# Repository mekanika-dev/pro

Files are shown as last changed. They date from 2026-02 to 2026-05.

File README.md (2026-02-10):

# Pro CNC (Mk2)

> A robust CNC machine for precise milling featuring ballscrews and prismatic linear rails for superior accuracy across different jobs and materials.

- [Assembly Guide & Documentation](https://support.mekanika.io/products/pro-cnc-mk2)
- [Shop](https://www.mekanika.io/en/store/be/pro/)
- [Contact](https://www.mekanika.io/contact-us/)

Mekanika Pro CNC (Mk2)

## Repository Structure

- **`bom/`** - Bill of Materials
- **`cad/`** - CAD files
- **`docs/`** - Documentation files

The Bill of Materials is available as a CSV file, which is dynamically updated from our ERP. We recommend using this **[web viewer](https://mekanika-dev.github.io/data-sync-actions/odoo/bom-viewer.html)** to browse its content.

All 3D assembly files are made in STEP format and compatible with many CAD software. Please note that you will need Git LFS installed to clone or pull the repo correctly, since these files exceed 100MB.

The design files can also be viewed in web browsers using these links:

- [Pro-S](https://a360.co/44uoy98)
- [Pro-M](https://a360.co/3PJz4Fp)
- [Pro-L](https://a360.co/46BXE0F)
- [Pro Control Unit](https://a360.co/4mlOA7u)

## Assembly Guide

The assembly guide is available on our [support website](https://support.mekanika.io/products/pro-cnc-mk2). If you have feedback or want to raise an issue about a specific assembly step, you can use the feedback buttons available on each step's page.

## Community

Mekanika encourages collaborative design and innovation. We welcome:

- Designers and engineers to contribute
- Feedback on design variations
- Any discussions around or products and potential improvements

Don't hesitate to join us on our [Discord](https://discord.gg/n7RsBtUdGc)

## License

This project is licensed under the **CERN Open Hardware Licence Version 2 - Strongly Reciprocal** ([CERN-OHL-S v2](https://ohwr.org/cern_ohl_s_v2.pdf))

For the complete license terms, see REUSE.toml

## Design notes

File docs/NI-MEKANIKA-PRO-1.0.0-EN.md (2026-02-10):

---
title: "USER MANUAL: CNC PRO"
css: style.css
---

<div class="cover-page" style="text-align: center;">

Logo Mekanika

<h4 style="margin-bottom: 0;">3-AXIS CNC MILLING MACHINE</h4>

<hr style="width: 200px; margin: 10px auto; color:#000 !important;"/>

<h4 style="margin-top: 0;">PRO MODEL V1.0</h4>

Pro ISO View

**ORIGINAL MANUAL**
<br/>
Version: 1.0.0-EN
<br/>
Revision Date: November 2025

</div>

## TABLE OF CONTENTS

#### 1. GENERAL INFORMATION

<ul style="list-style-type: none;">
  <li>1.1 <a href="#11-manufacturer-identification">Manufacturer identification</a></li>
  <li>1.2 <a href="#12-ce-declaration-of-conformity">CE Declaration of Conformity</a></li>
  <li>1.3 <a href="#13-intended-use">Intended use</a>
    <ul style="list-style-type: none;">
      <li>1.3.1 <a href="#131-normal-use">Normal use</a></li>
      <li>1.3.2 <a href="#132-prohibited-uses">Prohibited uses</a></li>
    </ul>
  </li>
  <li>1.4 <a href="#14-authorized-personnel">Authorized personnel</a>
    <ul style="list-style-type: none;">
      <li>1.4.1 <a href="#141-minimum-requirements">Minimum requirements</a></li>
      <li>1.4.2 <a href="#142-restrictions">Restrictions</a></li>
    </ul>
  </li>
</ul>

#### 2. SAFETY

<ul style="list-style-type: none;">
  <li>2.1 <a href="#21-safety-instructions-by-risk-level">Safety instructions by risk level</a></li>
  <li>2.2 <a href="#22-personal-protective-equipment">Personal protective equipment</a>
    <ul style="list-style-type: none;">
      <li>2.2.1 <a href="#221-mandatory-ppe">Mandatory PPE</a></li>
      <li>2.2.2 <a href="#222-dress-code">Dress code</a></li>
    </ul>
  </li>
  <li>2.3 <a href="#23-safety-devices">Safety devices</a>
    <ul style="list-style-type: none;">
      <li>2.3.1 <a href="#231-emergency-stop">Emergency stop</a></li>
      <li>2.3.2 <a href="#232-limit-switches">Limit switches</a></li>
      <li>2.3.3 <a href="#233-dust-shoe">Dust shoe</a></li>
    </ul>
  </li>
</ul>

#### 3. TECHNICAL DESCRIPTION

<ul style="list-style-type: none;">
  <li>3.1 <a href="#31-overview">Overview</a>
    <ul style="list-style-type: none;">
      <li>3.1.1 <a href="#311-axis-diagram">Axis diagram</a></li>
      <li>3.1.2 <a href="#312-control-box-diagram">Control box diagram</a></li>
    </ul>
  </li>
  <li>3.2 <a href="#32-technical-specifications">Technical specifications</a></li>
</ul>

#### 4. INSTALLATION & ASSEMBLY

<ul style="list-style-type: none;">
  <li>4.1 <a href="#41-unpacking-and-inspection">Unpacking and inspection</a>
    <ul style="list-style-type: none;">
      <li>4.1.1 <a href="#411-upon-receipt">Upon receipt</a></li>
      <li>4.1.2 <a href="#412-kit-inventory">Kit inventory</a></li>
    </ul>
  </li>
  <li>4.2 <a href="#42-assembly">Assembly</a>
    <ul style="list-style-type: none;">
      <li>4.2.1 <a href="#421-preparation">Preparation</a></li>
    </ul>
  </li>
  <li>4.3 <a href="#43-installation">Installation</a>
    <ul style="list-style-type: none;">
      <li>4.3.1 <a href="#431-recommended-layout">Recommended layout</a></li>
      <li>4.3.2 <a href="#432-room-requirements">Room requirements</a></li>
    </ul>
  </li>
</ul>

#### 5. INITIAL STARTUP

<ul style="list-style-type: none;">
  <li>5.1 <a href="#51-preliminary-checks">Preliminary checks</a>
    <ul style="list-style-type: none;">
      <li>5.1.1 <a href="#511-safety-checklist">Safety checklist</a></li>
    </ul>
  </li>
  <li>5.2 <a href="#52-first-power-on">First power on</a>
    <ul style="list-style-type: none;">
      <li>5.2.1 <a href="#521-startup-sequence">Startup sequence</a></li>
    </ul>
  </li>
  <li>5.3 <a href="#53-functional-test">Functional test</a></li>
</ul>

#### 6. OPERATION

<ul style="list-style-type: none;">
  <li>6.1 <a href="#61-checklist-for-safe-machine-operation">Checklist for safe machine operation</a>
    <ul style="list-style-type: none;">
      <li>6.1.1 <a href="#611-daily-startup">Daily startup</a></li>
    </ul>
  </li>
  <li>6.2 <a href="#62-workpiece-clamping">Workpiece clamping</a>
    <ul style="list-style-type: none;">
      <li>6.2.1 <a href="#621-fixation-systems-supplied-with-base-kit">Fixation systems supplied with base kit</a></li>
      <li>6.2.2 <a href="#622-fixation-rules">Fixation rules</a></li>
    </ul>
  </li>
  <li>6.3 <a href="#63-tool-installation">Tool installation</a>
    <ul style="list-style-type: none;">
      <li>6.3.1 <a href="#631-tool-change">Tool change</a></li>
      <li>6.3.2 <a href="#632-tool-length-measurement">Tool length measurement</a></li>
    </ul>
  </li>
  <li>6.4 <a href="#64-programming-and-machining">Programming and machining</a>
    <ul style="list-style-type: none;">
      <li>6.4.1 <a href="#641-accepted-formats">Accepted formats</a></li>
      <li>6.4.2 <a href="#642-operating-modes">Operating modes</a></li>
    </ul>
  </li>
  <li>6.5 <a href="#65-monitoring-during-machining">Monitoring during machining</a>
    <ul style="list-style-type: none;">
      <li>6.5.1 <a href="#651-control-points">Control points</a></li>
      <li>6.5.2 <a href="#652-anomalies-and-actions">Anomalies and actions</a></li>
    </ul>
  </li>
</ul>

#### 7. ADD-ONS AND OPTIONS

<ul style="list-style-type: none;">
  <li>7.1 <a href="#71-vacuum-table">Vacuum table</a>
    <ul style="list-style-type: none;">
      <li>7.1.1 <a href="#711-specifications">Specifications</a></li>
      <li>7.1.2 <a href="#712-operation">Operation</a></li>
    </ul>
  </li>
  <li>7.2 <a href="#72-dust-collection-kit">Dust collection kit</a>
    <ul style="list-style-type: none;">
      <li>7.2.1 <a href="#721-specifications">Specifications</a></li>
    </ul>
  </li>
  <li>7.3 <a href="#73-laser-module-lsr">Laser module (LSR)</a>
    <ul style="list-style-type: none;">
      <li>7.3.1 <a href="#731-specifications">Specifications</a></li>
    </ul>
  </li>
</ul>

#### 8. MAINTENANCE & TROUBLESHOOTING

<ul style="list-style-type: none;">
  <li>8.1 <a href="#81-preventive-maintenance-plan">Preventive maintenance plan</a></li>
  <li>8.2 <a href="#82-lubrication">Lubrication</a></li>
  <li>8.3 <a href="#83-spare-parts">Spare parts</a></li>
</ul>

#### 9. TROUBLESHOOTING

<ul style="list-style-type: none;">
  <li>9.1 <a href="#91-troubleshooting-and-diagnostics">Troubleshooting and diagnostics</a></li>
  <li>9.2 <a href="#92-technical-support">Technical support</a>
    <ul style="list-style-type: none;">
      <li>9.2.1 <a href="#921-before-contacting-support">Before contacting support</a></li>
    </ul>
  </li>
</ul>

#### 10. TRANSPORTATION & STORAGE

<ul style="list-style-type: none;">
  <li>10.1 <a href="#101-machine-transportation">Machine Transportation</a></li>
  <li>10.2 <a href="#102-packaging--waste">Packaging & Waste</a></li>
  <li>10.3 <a href="#103-storage">Storage</a></li>
</ul>

## 1. GENERAL INFORMATION {#1-general-information}

### 1.1 Manufacturer identification {#11-manufacturer-identification}

**Mekanika SRL**

Chaussée de Mons 1281  
1070 Anderlecht, Belgium  
VAT No: BE0740501760

**Contact:**

<ul style="list-style-type: none;">
<li><i class="fas fa-envelope" style="color: #2196f3;"></i> info@mekanika.io</li>
<li><i class="fas fa-globe" style="color: #2196f3;"></i> www.mekanika.io</a></li>
</ul>

### 1.2 CE Declaration of Conformity {#12-ce-declaration-of-conformity}

This machine complies with the following European directives:

- **2006/42/EC** - Machinery Directive
- **2014/30/EU** - Electromagnetic Compatibility (EMC) Directive

**Applied harmonized standards:**

- **EN ISO 12100:2010** - Safety of machinery, General principles
- **EN 60204-1:2006** - Electrical safety of machinery
- **EN ISO 13850:2015** - Emergency stop function
- **EN 848-3:2012** - Safety of woodworking machines (partially)
- **EN 61000-6-1** - EMC Immunity
- **EN 61000-6-3** - EMC Emissions

The original declaration of conformity is provided with this machine.

### 1.3 Intended use {#13-intended-use}

Please read this operating manual and all accompanying documents in their entirety before commissioning the machine.

If in doubt or if you need additional information, do not hesitate to contact us before using the machine.

#### 1.3.1 Normal use {#131-normal-use}

The MEKANIKA PRO CNC milling machine is a 3-axis CNC machine designed for:

<ul style="list-style-type: none; margin-left: 0.75em">
  <li><i class="fas fa-square-check" style="color: #4EBD7D;"></i> Machining wood and derivatives (plywood, MDF, OSB)</li>
  <li><i class="fas fa-square-check" style="color: #4EBD7D;"></i> Machining plastics (PVC, acrylic, polycarbonate)</li>
  <li><i class="fas fa-square-check" style="color: #4EBD7D;"></i> Machining non-ferrous metals (aluminum, brass)</li>
  <li><i class="fas fa-square-check" style="color: #4EBD7D;"></i> Machining composite materials (with special precautions)</li>
</ul>

#### 1.3.2 Prohibited uses {#132-prohibited-uses}

The following uses are **PROHIBITED**:

<ul style="list-style-type: none; margin-left: 0.75em">
  <li><i class="fas fa-xmark" style="color: #d32f2f;"></i> Machining unknown composite materials or those containing asbestos</li>
  <li><i class="fas fa-xmark" style="color: #d32f2f;"></i> Use in explosive atmospheres</li>
  <li><i class="fas fa-xmark" style="color: #d32f2f;"></i> Outdoor use or in humid environments</li>
  <li><i class="fas fa-xmark" style="color: #d32f2f;"></i> Machining improperly secured workpieces</li>
  <li><i class="fas fa-xmark" style="color: #d32f2f;"></i> Machining beyond the machine's technical capabilities</li>
</ul>

### 1.4 Authorized personnel {#14-authorized-personnel}

#### 1.4.1 Minimum requirements {#141-minimum-requirements}

- **Minimum age:** 16 years
- **Required training:**
  - Complete reading of this manual
  - Completed online training (series of free video tutorials)
  - Basic CAM knowledge
- **Physical abilities:**
  - Normal or corrected vision
  - Normal or aided hearing
  - Sufficient mobility to access the emergency stop

#### 1.4.2 Restrictions {#142-restrictions}

- Prohibited for untrained persons
- Prohibited for persons under influence (alcohol, drugs, medication)
- Mandatory supervision for persons learning to operate the machine

## 2. SAFETY {#2-safety}

Read the entire operating manual to familiarize yourself with the machine's features and how to use them. Improper operation of the machine can result in damage to the machine, your personal property, and cause serious injury, electric shock and/or fire.

**It is imperative to comply at all times with the safety instructions listed in this operating manual.**

### 2.1 Safety instructions by risk level {#21-safety-instructions-by-risk-level}

The following terms are used in this operating manual to indicate different levels of potential danger when using this machine. Safety symbols and their explanations require your attention.

Safety warnings do not eliminate any danger. The instructions or warnings they provide do not replace appropriate preventive measures.

> **<i class="fas fa-ban" style="color: #d32f2f;"></i> DANGER** - _Instructions which, if not properly followed, create a probability of property damage, collateral damage, serious injury or death, or create a high probability of superficial injury._

| **RISK TYPE** | **SAFETY INSTRUCTIONS** |
| :--- | :--- |
| **Risk of electrocution** | Machine plugs must match the power outlet used. Never modify the plug in any way. Do not use adapter plugs with grounded machines. |
| **Risk of electrocution - indirect contact** | An insulation fault can energize normally non-conductive metal parts (chassis, structure, housing). Causes include: cable wear in cable carriers, moisture infiltration, accumulation of conductive dust, failed components, or mechanical damage. Never use the machine if: <br/> - The differential circuit breaker trips repeatedly; <br/> - Electric arc traces are visible (blackening, burning smell); <br/> - Moisture/condensation is visible in the housing. |
| **Toxic dust** | Some dust created when machining certain types of materials may contain chemicals known to cause cancer, birth defects or other reproductive harm. Always research the material you have on hand before machining it. Here are some examples of these chemicals: lead from non-ferrous metals containing lead, carbonate from carbon fiber, arsenic and chromium from chemically treated wood.<br><br>The risk you run from exposure varies depending on how often you perform this type of work. To reduce your exposure to these chemicals: work in a well-ventilated area and use approved safety equipment, such as dust masks specifically designed to filter microscopic particles. |
| **Explosive atmosphere** | Do not operate the machine in explosive atmospheres, such as in the presence of flammable liquids, gases or dust. Machines can create sparks that can ignite dust or fumes. |

> **<i class="fas fa-exclamation-triangle" style="color: #ff9800;"></i> WARNING** - _Instructions which, if not properly followed, create a probability of property damage and a possibility of serious injury._

| **RISK TYPE** | **SAFETY INSTRUCTIONS** |
| :--- | :--- |
| **Dress code** | Dress appropriately. Do not wear loose clothing or jewelry. Pin your hair above your shoulders so it cannot get caught in linear guides or moving parts. |
| **Vigilance** | Stay alert, watch what you are doing and use common sense when operating a machine. Do not use a machine when you are tired and/or under the influence of drugs, alcohol or medication. A moment of inattention when using a machine can result in serious injury. |
| **Personal protection**  | Use personal protective equipment. Always wear eye protection. Protective equipment, such as a dust mask or appropriate hearing protection, reduces the risk of injury. |
| **Machine control** | This machine is computer controlled. During operation, it cannot be directly controlled. Lack of caution or expertise and program errors can lead to unexpected movements. |
| **Rotating tool** | Do not touch the rotating tool area. The proximity of the rotating tool to your hand is not always easy to detect. |
| **Tool jam** | If the workpiece or end mill jams, immediately press the emergency stop button. Wait until all moving parts have stopped and the spindle is off, then release the stuck material. Do not attempt to do this while the spindle is running. |
| **Hot tools** | Do not touch the end mill or collet after use. After use, they are too hot to touch with bare hands. |
| **Hot surfaces** | Do not touch the motors, as they can heat up during machine operation. |
| **Tool handling** | Be careful when handling tools, they can be very sharp. Never place any part of the tool or accessories in your mouth, as this can result in serious injury. |
| **Workpiece fixation** | Before starting any machining operation, always secure your workpiece properly. Never try to hold the workpiece by hand or with accessories. These tools can easily jam in the material and can kick back, resulting in loss of control and serious injury. |
| **Limit sensors** | Never try to reach the limit sensors when the machine is moving, this could result in crushing your hand or fingers. |
| **Prohibited modifications** | Do not modify your machine, or use it in a manner not intended by the manufacturer. Any alteration or modification constitutes misuse and can result in serious injury. |
| **Lockout** | Disconnect the plug from the power source before making adjustments, changing accessories or disassembling the machine. |
| **Machine access** | Keep the machine out of reach of children and do not allow persons unfamiliar with these instructions to use the machine. Machines are dangerous in the hands of untrained users. |
| **Safety distance** | Keep children and bystanders at a distance. Distractions can cause you to lose control and cause accidents. |

> **<i class="fas fa-info-circle" style="color: #2196f3;"></i> CAUTION** - _Instructions which, if not properly followed, create a possibility of property damage and a possibility of minor injury._

| **RISK TYPE** | **SAFETY INSTRUCTIONS** |
| :--- | :--- |
| **Mandatory training** | All persons using the machine must have read and fully understood all relevant safety and operating instructions. Any misunderstanding can result in injury. |
| **Cleanliness and lighting** | Keep the work area clean and well lit. Cluttered or dark areas are prone to accidents. |
| **Indoor use** | Only operate the machine in indoor spaces. |
| **Moisture protection** | Do not expose the machine to moisture. The machine can only be used indoors. |
| **Supervision** | Do not leave the machine running unattended, and cut the spindle power if you leave. The machine is only secure when it is completely stopped and unplugged from the mains. |
| **Proper use** | Use the machine and its accessories in accordance with this manual, taking into account the working conditions and the work to be performed. Using the machine for operations other than those intended can result in a dangerous situation with a high probability of injury. |
| **Tool condition** | Never use dull or damaged end mills. Damaged end mills can break during use. Dull end mills require more force to cut, which can result in end mill breakage. |
| **Machining parameters** | The speed and feed rate of the end mill during engraving, profiling or cutting are very important. Always follow the recommended speed and feed rate for a particular end mill/machine/operation configuration. |
| **Ventilation** | Remember to clean the ventilation openings of the control boxes using compressed air. Excessive dust accumulation inside the boxes can cause electrical failures. |
| **Preventive maintenance** | Properly maintain the tools you use. Check for misalignment or binding of moving parts, broken parts and any other condition that may affect the machine's operation. If damaged, have the machine repaired before using it. Many accidents are caused by poorly maintained machines. |
| **Repairs** | Have your machine repaired by a qualified repairer using only identical spare parts. |

### 2.2 Personal protective equipment {#22-personal-protective-equipment}

#### 2.2.1 Mandatory PPE {#221-mandatory-ppe}

| Equipment | Use | Pictogram |
| :--- | :--- | :---: |
| **Safety glasses** | Recommended during machining |  Safety glasses  |
| **Hearing protection** | Recommended during machining, mandatory if noise level > 80 dB(A) | Hearing protection |
| **Gloves** | Recommended when handling parts/tools | Gloves |
| **FFP2 mask** | Mandatory when machining composite materials | FFP2 mask |
| **Safety shoes** | Recommended for all work in front of a machine | Safety shoes |

#### 2.2.2 Dress Code {#222-dress-code}

**<i class="fas fa-square-check" style="color: #4EBD7D;"></i> MANDATORY:**

- Fitted clothing
- Short sleeves or rolled up
- Long hair tied back or under cap

**<i class="fas fa-xmark" style="color: #d32f2f;"></i> PROHIBITED:**

- Jewelry (rings, necklaces, bracelets)
- Loose clothing
- Ties, scarves
- Gloves during machining

### 2.3 Safety devices {#23-safety-devices}

#### 2.3.1 Emergency stop {#231-emergency-stop}

**Characteristics:**

- Type: Lockable mushroom button
- Color: Red on yellow background
- Standard: EN ISO 13850:2015
- Position: Front face, easily accessible

**Operation:**

1. **Activation:** Press the red button
   - Immediate stop of all movements
   - Spindle shutdown
   - Machine control software lockout
2. **Reset:** Turn the button clockwise
   - The program must be restarted manually

#### 2.3.2 Limit switches {#232-limit-switches}

**Configuration:**

- 6 NC PNP inductive sensors
- 2 sensors on X and Y axes (min/max) with AND logic for redundant safety

**Triple function:**

1. **Homing:** Machine referencing at startup
2. **Safety:** Emergency stop if limit reached
3. **Square gantry:** Gantry squaring

#### 2.3.3 Dust shoe {#233-dust-shoe}

**Dual function:**

- Protection against tool access
- Chip and dust collection

> **<i class="fas fa-info-circle" style="color: #2196f3;"></i> CAUTION** - _Never remove the shoe during machining_

## 3. TECHNICAL DESCRIPTION {#3-technical-description}

### 3.1 Overview {#31-overview}

The MEKANIKA PRO is a 3-axis CNC milling machine, allowing material to be machined by moving along the X, Y and Z axes, or a combination of these by linear interpolation.

#### 3.1.1 Axis diagram {#311-axis-diagram}

Axes diagram

**Axes terminology:**

- **X axis:** Lateral movement (left-right)
- **Y axis:** Longitudinal movement (front-back)
- **Z axis:** Vertical movement (up-down)

#### 3.1.2 Control box diagram {#312-control-box-diagram}

Control box diagram

**Connector description:**

- **1**: Fan
- **2**: Motors
- **3**: Limit switches
- **4**: Emergency stop
- **5**: Tool probe (Input 1)
- **6**: Spindle control
- **7**: Input 2
- **8**: Input 3
- **9**: Laser control
- **10**: HDMI
- **11**: USB 2.0
- **12**: Ethernet
- **13**: Power supply
- **14**: Ground

### 3.2 Technical specifications {#32-technical-specifications}

| **CHARACTERISTIC** | **VALUE** |
| :--- | :--- |
| **MACHINE DIMENSIONS** | |
| Overall dimensions | - S: 960 x 960 x 650 mm <br/> - M: 1360 x 960 x 650 mm <br/> - L: 1250 x 1250 x 650 mm |
| Total weight | - S: 55 kg <br/> - M: 62 kg <br/> - L: 69 kg |
| **WORKING AREA** | |
| Machinable surface | - S: 630 x 630 mm <br/> - M: 630 x 1030 mm <br/> - L: 1030 x 1030 mm |
| Table-spindle distance (max) | 105 mm |
| **PERFORMANCE** | |
| Max travel speed | 10000 mm/min |
| Recommended machining speed | 100 - 7000 mm/min |
| **MECHANICS** | |
| Linear guides | Double prismatic rail HGR20 |
| X, Y & Z transmission | 16 mm ball screws (C7) |
| Structure | Aluminum profiles + steel plates |
| **MOTORS** | |
| X, Y & Z motors | NEMA23 5A |
| **SPINDLE** | |
| Power | 2.2 kW |
| Cooling | Air |
| Rotation speed | 6000 - 24000 rpm |
| Collet | ER20 (1-13 mm) |
| Control | Variable frequency drive (VFD) |
| **ELECTRICAL** | |
| Power supply | 230V AC single phase, 50 Hz |
| Maximum power | 2.9 kW |
| Protection | 16A fuse, grounding mandatory |
| **ENVIRONMENT** | |
| Operating temperature | 5°C to 35°C |
| Relative humidity | 40-60% |
| Use | Indoor only |

## 4. INSTALLATION & ASSEMBLY {#4-installation--assembly}

### 4.1 Unpacking and inspection {#41-unpacking-and-inspection}

#### 4.1.1 Upon receipt {#411-upon-receipt}

**Check immediately:**

1. Condition of packaging (photos if damaged)
2. Presence of all packages (see delivery note)
3. Absence of apparent damage

#### 4.1.2 Kit inventory {#412-kit-inventory}

We strongly recommend that you inventory your kit before starting assembly. The list of parts grouped by package is available on our website:
<br>
<i class="fas fa-globe" style="color: #2196f3;"></i> [support.mekanika.io/products/pro-cnc-mk2/kit-content](https://support.mekanika.io/products/pro-cnc-mk2/kit-content)

### 4.2 Assembly {#42-assembly}

Please carefully follow our online assembly guide to properly assemble your Mekanika machine.
<br>
<i class="fas fa-globe" style="color: #2196f3;"></i> [support.mekanika.io/products/pro-cnc-mk2/assembly-guide](https://support.mekanika.io/products/pro-cnc-mk2/assembly-guide)

#### 4.2.1 Preparation {#421-preparation}

- **Required space:**
  - S: 1.96 × 1.96 m minimum
  - M: 2.36 x 1.96 m minimum
  - L: 2.36 x 2.36 m minimum
- **Estimated time:** 12 hours (alone) - 7 hours (2 people)
- **Required tools:** Supplied in the kit

> **<i class="fas fa-exclamation-triangle" style="color: #ff9800;"></i> RISK** - There is a non-negligible risk of heavy items falling during assembly. Please handle heavy parts with at least 2 people.

> **<i class="fas fa-info-circle" style="color: #2196f3;"></i> CAUTION** - Please follow the precise order of assembly steps to avoid risks of machine malfunction.

### 4.3 Installation {#43-installation}

#### 4.3.1 Recommended layout {#431-recommended-layout}

If you have the "table support" accessory, place the machine on a regular and stable floor.
If you do not have a "table support", place the machine on a robust and stable table allowing you to work at a good height. To ensure a comfortable working height, we recommend a working height of approximately 85 cm.

All moving parts of the machine must be able to operate without collision.

The machine must be easily accessible and usable. In particular, the emergency stop button must be easily accessible at all times.

**Zone description:**

- **1**: Operating zone
- **2**: Loading zone
- **3**: Maintenance and safety zone

Working area

#### 4.3.2 Room requirements {#432-room-requirements}

**Floor:**

- Flatness: < 5 mm/m
- Capacity: > 200 kg/m²
- Type: Concrete (recommended)

**Environment:**

- Temperature: 18-25°C ideal
- Humidity: 40-60%
- Lighting: > 500 lux on work area
- Ventilation: Adequate air renewal

## 5. INITIAL STARTUP {#5-initial-startup}

Before commissioning, the machine and all connected components must be properly wired and in perfect condition.

The operator must have read and understood the complete documentation for the relevant machine model and the corresponding instructions. In addition, they must have been trained in the operation of the machine and its accessories and must be familiar with the use of the CNC milling machine and PlanetCNC software in general.

### 5.1 Preliminary checks {#51-preliminary-checks}

> **<i class="fas fa-info-circle" style="color: #2196f3;"></i> CAUTION** - Never power on before these checks

#### 5.1.1 Safety checklist {#511-safety-checklist}

**Mechanical:**

<ul style="list-style-type: none; margin-left: 0.75em">
  <li><i class="fas fa-square-check" style="color: #4EBD7D;"></i> All fasteners tightened</li>
  <li><i class="fas fa-square-check" style="color: #4EBD7D;"></i> Freedom of axis movement (manual rotation)</li>
  <li><i class="fas fa-square-check" style="color: #4EBD7D;"></i> No abnormal play</li>
  <li><i class="fas fa-square-check" style="color: #4EBD7D;"></i> Guides and ball screws lubricated</li>
</ul>

**Electrical:**

<ul style="list-style-type: none; margin-left: 0.75em">
  <li><i class="fas fa-square-check" style="color: #4EBD7D; "></i> Ground continuity (< 0.1 Ω)</li>
  <li><i class="fas fa-square-check" style="color: #4EBD7D;"></i> Cable insulation</li>
  <li><i class="fas fa-square-check" style="color: #4EBD7D;"></i> Connections tight</li>
  <li><i class="fas fa-square-check" style="color: #4EBD7D;"></i> Mains differential protection tested</li>
</ul>

**Safety:**

<ul style="list-style-type: none; margin-left: 0.75em">
  <li><i class="fas fa-square-check" style="color: #4EBD7D;"></i> Emergency stop accessible and functional</li>
  <li><i class="fas fa-square-check" style="color: #4EBD7D;"></i> Limit switches connected</li>
  <li><i class="fas fa-square-check" style="color: #4EBD7D;"></i> Dust shoe installed</li>
  <li><i class="fas fa-square-check" style="color: #4EBD7D;"></i> Work area clear</li>
</ul>

### 5.2 First power on {#52-first-power-on}

#### 5.2.1 Startup sequence {#521-startup-sequence}

**1. Preparation**

- Area clear in front of and around the machine
- PPE worn
- Documentation within reach

**2. Power on**

- Check that emergency stop is unlocked
- Turn on control box
- Wait for Raspberry Pi initialization
- Wait for PlanetCNC to launch

**3. Initial checks**

- Control box fans rotating
- Limit switch indicators lit
- Touch screen on and PlanetCNC interface active
- Emergency stop button functional

### 5.3 Functional test {#53-functional-test}

We strongly recommend following our illustrated machine startup guide, available on our website:
<br>
<i class="fas fa-globe" style="color: #2196f3;"></i> [https://support.mekanika.io/products/pro-cnc-mk2/get-started](https://support.mekanika.io/products/pro-cnc-mk2/get-started)

This includes all the necessary information to test the machine on first use, as well as useful information about its operation and safety functions.

## 6. OPERATION {#6-operation}

The Pro CNC milling machine is intended for regular and professional use. Thanks to the machine's rigidity, it is possible to process a variety of different materials, such as wood and non-ferrous metals.

The plausible and reasonable scope of uses includes:

- Manual movement mode, using a digital "jog" to move the machine along its 3 axes independently.
- The automatic positioning procedure, performed by the user by clicking a digital button. This procedure moves the machine sequentially on each of its axes in the following order: Z, X, Y, until it encounters the limit switches.
- The tool length measurement procedure, activated by the user by clicking a digital button. This procedure lowers the machine at reduced speed along its Z axis until its tool contacts a removable sensor previously placed by the user.
- Normal operating mode, where the machine moves automatically according to a machine language, called G-code, previously loaded by the user.
- Manual control mode using a terminal allowing the machine to move according to a machine language, called G-code, entered directly by the user.

The plausible and reasonable scope of interventions includes:

- Manual movement of the machine to access certain areas.
- Changing the tool on the spindle.
- Attaching or removing the dust shoe.
- Attaching or removing the material to be machined.
- Launching, pausing and stopping the G-Code.
- Connecting/disconnecting external machine cables.
- Opening cable chains to access the machine.

### 6.1 Checklist for safe machine operation {#61-checklist-for-safe-machine-operation}

#### 6.1.1 Daily startup {#611-daily-startup}

**1. Inspection and equipment**

- Inspect equipment to ensure there are no obvious defects, damaged chucks, dull or cracked tools
- Use appropriate PPE (glasses, helmet, ...)
- Tie back long hair and wear well-fitted clothing and roll up your sleeves to avoid snags

**2. Machine preparation**

- Check where the emergency stop button is located
- Never connect or disconnect cables from the electronic box when the device is powered on
- Make sure the workpiece is firmly and securely clamped
- Check that the end mill is sharp and firmly tightened in the spindle chuck
- When handling or changing end mills, avoid touching the cutting edges
- Keep your hands free during manual adjustments

**3. During use**

- Never touch the machine when it is running and keep your hands away from any moving parts during machining
- Stay away from the machine when it is operational

**4. After machining**

- Use a brush or vacuum to clean chips from surfaces
- If linear guides and ball screws are dusty, blow them with compressed air to keep them clean and unobstructed by chips
- Clean the floor and work area around the machine
- Clean and store personal protective equipment
- Mark any defective equipment and contact us if you encounter a problem

**5. Normal shutdown**

1. Complete machining in progress
2. Stop the spindle
3. **Shut down Raspberry Pi** (proper shutdown)
4. Wait 30 seconds
5. Turn off control box

> **<i class="fas fa-info-circle" style="color: #2196f3;"></i> CAUTION** - Follow the order to avoid Raspberry Pi SD card corruption

**6. Emergency stop**

**In case of danger:**

1. **Immediately press** the red button
2. Cut power if necessary
3. Analyze the situation
4. Correct the problem
5. Reset (turn the button)
6. Redo a homing procedure

### 6.2 Workpiece clamping {#62-workpiece-clamping}

#### 6.2.1 Fixation systems supplied with base kit {#621-fixation-systems-supplied-with-base-kit}

**Wood screws:**

- For soft materials
- Direct screwing into spoilerboard
- Regular spacing

**Clamps with inserts:**

- For all materials
- M6 inserts in spoilerboard

#### 6.2.2 Fixation rules {#622-fixation-rules}

**<i class="fas fa-square-check" style="color: #4EBD7D;"></i> GOOD PRACTICES:**

- Minimum 4 fixation points
- Symmetrical distribution
- Verification before machining

**<i class="fas fa-xmark" style="color: #d32f2f;"></i> PROHIBITIONS:**

- Manual fixation
- Adhesive alone
- Cantilevered workpiece
- Excessive clamping (deformation)

> **<i class="fas fa-ban" style="color: #d32f2f;"></i> DANGER** - During machining, NEVER hold the workpiece by hand

### 6.3 Tool installation {#63-tool-installation}

#### 6.3.1 Tool change {#631-tool-change}

**Procedure:**

1. Wait for complete stop or machine pause
2. Move Z axis to high position
3. Unlock ER20 nut (keys provided)
4. Remove tool (gloves strongly recommended)
5. Insert new tool
6. Tighten firmly (without excess)

#### 6.3.2 Tool length measurement {#632-tool-length-measurement}

**With the supplied tool probe:**

1. Place the probe on the workpiece or spoilerboard (depending on the Z0 coordinate defined in the program)
2. Position the spindle above the probe
3. Press the tool length measurement icon
4. Slow automatic descent
5. Contact and memorization of the new Z0 position

### 6.4 Programming and machining {#64-programming-and-machining}

#### 6.4.1 Accepted formats {#641-accepted-formats}

- **G-code:** .nc, .ngc, .gcode
- **Generation:** Via any CAM software. Some examples:
  - Fusion 360 (recommended)
  - VCarve
  - FreeCAD
  - Others

#### 6.4.2 Operating modes {#642-operating-modes}

**Automatic mode:**

1. Load the G-code file
2. Check the simulation in PlanetCNC
3. Position the workpiece origin (X0 Y0 Z0)
4. Start the program (Start)

**Manual mode (JOG):**

- Movement by axes
- Variable speed (10-100%)
- Incremental movement possible (examples: 0.01, 0.1, 1, 10 mm)

**MDI mode:**

- Direct G-code command sending
- Sequence testing
- Precise positioning

### 6.5 Monitoring during machining {#65-monitoring-during-machining}

#### 6.5.1 Control points {#651-control-points}

- Abnormal vibrations
- Unusual noise
- Chip quality
- Temperature near tool
- Workpiece fixation

#### 6.5.2 Anomalies and actions {#652-anomalies-and-actions}

| Anomaly | Probable cause | Immediate action |
| :--- | :--- | :--- |
| **Vibrations** | Worn tool or inappropriate parameters | STOP → Check tool and parameters |
| **Smoke** | Worn tool or inappropriate parameters | EMERGENCY → Stop |
| **Loud noise** | Very worn or broken tool | EMERGENCY → Stop |
| **Moving workpiece** | Insufficient fixation | EMERGENCY → Stop |

> In case of doubt → **IMMEDIATE STOP**

## 7. ADD-ONS AND OPTIONS {#7-add-ons-and-options}

### 7.1 Vacuum table {#71-vacuum-table}

#### 7.1.1 Specifications {#711-specifications}

- Plastic plenum with dedicated spoilerboard and integrated seals
- 3 to 5 independent zones (depending on machine size)
- Vacuum pump and connections
- Installation: 2 hours

#### 7.1.2 Operation {#712-operation}

**New clamping system for workpieces:**

1. Place the workpiece on the spoilerboard
2. Open the necessary zones
3. Activate vacuum pump
4. Check hold (manual test)

Information about the kit and assembly guide can be found on our website:

<i class="fas fa-globe" style="color: #2196f3;"></i> [support.mekanika.io/products/vacuum-table/vacuum-table-evo-pro](https://support.mekanika.io/products/vacuum-table/vacuum-table-evo-pro)

We strongly recommend following our illustrated startup guide, dedicated to the vacuum table.

### 7.2 Dust collection kit {#72-dust-collection-kit}

#### 7.2.1 Specifications {#721-specifications}

- Anti-static suction hose Ø100mm
- Compatible with most workshop vacuums
- Pivoting tubular steel support
- Installation: 1 hour

Information about the kit and assembly guide can be found on our website:

<i class="fas fa-globe" style="color: #2196f3;"></i> [support.mekanika.io/products/dust-collection-kit](https://support.mekanika.io/products/dust-collection-kit)

### 7.3 Laser module (LSR) {#73-laser-module-lsr}

#### 7.3.1 Specifications {#731-specifications}

- Model: PLH3D-XT-50
- Power: 6W optical
- Wavelength: 445 nm (blue)
- Laser class: 4

> **<i class="fas fa-ban" style="color: #d32f2f;"></i> DANGER - CLASS 4 LASER**
>
> **Dedicated documentation:** See separate manual supplied with the machine

Information about the kit and assembly guide can be found on our website:

<i class="fas fa-globe" style="color: #2196f3;"></i> [support.mekanika.io/products/laser-head-6w](https://support.mekanika.io/products/laser-head-6w)

## 8. MAINTENANCE & TROUBLESHOOTING {#8-maintenance--troubleshooting}

We strongly recommend following our video maintenance guide, available on our website:

<i class="fas fa-globe" style="color: #2196f3;"></i> [support.mekanika.io/products/pro-cnc/maintenance](https://support.mekanika.io/products/pro-cnc-mk2/maintenance)

### 8.1 Preventive maintenance plan {#81-preventive-maintenance-plan}

| **FREQUENCY** | **OPERATION** | **DURATION** | **MACHINE STOP** |
| :--- | :--- | :--- | :--- |
| **Daily** | Chip cleaning | 10 min | No |
| **Daily** | General visual inspection | 5 min | No |
| **Monthly** | Lubrication of X/Y/Z guides | 15 min | Yes |
| **Monthly** | Control box filter cleaning | 10 min | Yes |
| **Monthly** | Ball screw greasing | 15 min | Yes |
| **Monthly** | Mechanical play check on linear systems | 30 min | Yes |
| **Monthly** | Complete fastener check | 45 min | Yes |
| **Annual** | Complete machine overhaul | 4h | Yes |
| **Annual** | Possible bearing replacement | 2h | Yes |
| **Annual** | Geometric calibration | 2h | Yes |

### 8.2 Lubrication {#82-lubrication}

A linear system must be sufficiently lubricated to operate properly and avoid excessive wear or overheating. The required lubrication interval is determined by environmental conditions.

In general, lubrication is necessary every 100 to 200 hours of operation. We recommend using lithium-based greases, which perform well in high-load applications and have good oxidation stability.

**Procedure:**

1. Clean before greasing (cloth and isopropyl alcohol)
2. Apply grease moderately
3. Perform 10 complete machine travel cycles
4. Wipe excess grease

### 8.3 Spare parts {#83-spare-parts}

All machine and control box parts can be purchased individually as spare parts.

Please contact us directly about this.

When ordering spare parts, please provide information about the machine model, size and part number available according to the construction instructions.

## 9. TROUBLESHOOTING {#9-troubleshooting}

### 9.1 Troubleshooting and diagnostics {#91-troubleshooting-and-diagnostics}

If you have a problem with your machine, please consult our troubleshooting guides available online:

<i class="fas fa-globe" style="color: #2196f3;"></i> [https://support.mekanika.io/products/pro-cnc-mk2/troubleshoot](https://support.mekanika.io/products/pro-cnc-mk2/troubleshoot)

### 9.2 Technical support {#92-technical-support}

#### 9.2.1 Before contacting support {#921-before-contacting-support}

**Information to prepare:**

- Machine model (PRO)
- Machine serial number (located under the control box)
- Order number
- Problem description
- Photos/videos if possible

#### **CONTACT FORM**

<i class="fas fa-globe" style="color: #2196f3;"></i> [www.mekanika.io/en/contact-support](https://www.mekanika.io/en/contact-support)

## 10. TRANSPORTATION & STORAGE {#10-transportation--storage}

### 10.1 Machine Transportation {#101-machine-transportation}

If you wish to transport the machine, pay particular attention to its dimensions and weight, you may need additional people for transport.

Never lift heavy loads above people.

Avoid unilaterally loading the machine chassis during transport.

### 10.2 Packaging & Waste {#102-packaging--waste}

If you do not wish to reuse the device packaging, please sort it according to local sorting rules and take it to a waste collection center for recycling.

If you need to replace certain machine components, or put it out of service, please go to your local waste disposal center and proceed with selective sorting.

| **Material** | **Components** | **Channel** |
| :--- | :--- | :--- |
| **Aluminum** | Profile structure | Metal recycling  |
| **Steel** | Connection plates, axes, fasteners | Metal recycling  |
| **Electronics** | Control boards, motors | WEEE\* |
| **Cables** | Sheathed copper | WEEE\* |
| **Plastics** | Cable chains, connection plates | Plastic sorting  |

\* _Waste Electrical and Electronic Equipment_

### 10.3 Storage {#103-storage}

If the machine or its components are not used for an extended period, please observe the following points regarding storage:

- Store the machine and its components only in closed rooms
- Protect the machine and its components from moisture, cold, heat and direct solar radiation
- Store the machine and its components away from dust and cover if necessary
- The storage location should not be subject to vibrations.

---

**END OF INSTRUCTION MANUAL**

This manual is the property of MEKANIKA SRL. Any reproduction, even partial, is prohibited without written authorization.

<br/>

**IMPORTANT NOTES:**

- This manual must remain with the machine
- In case of resale, transmit all documents
- Updates available on [support.mekanika.io/download-center/cnc-milling](www.mekanika.io/en/contact-support)
- For any questions: info@mekanika.io

<br/>

**Keep this manual for future reference**

---

**© 2025 MEKANIKA SRL - All rights reserved**

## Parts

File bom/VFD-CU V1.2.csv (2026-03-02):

level | component_reference | component_name | component_quantity | parent_bom_reference | parent_bom_name | has_child_bom
0 | M00353 | VFD - 2.2kW Inverter Control Unit | 1.00 |  |  | True
1 | M00004 | 220V Inverter | 1.00 | M00353 | VFD - 2.2kW Inverter Control Unit | False
1 | M00355 | CNC Pro/Fab - Steel Parts - VFD Base | 1.00 | M00353 | VFD - 2.2kW Inverter Control Unit | False
1 | M00356 | CNC Pro/Fab - Steel Parts - VFD Cover | 1.00 | M00353 | VFD - 2.2kW Inverter Control Unit | False
1 | M00406 | Circuit Breaker 15A 250V AC | 1.00 | M00353 | VFD - 2.2kW Inverter Control Unit | False
1 | M00720 | Panel Mount IEC C14 Connector with RFI Filter, 15A 250V | 1.00 | M00353 | VFD - 2.2kW Inverter Control Unit | False
1 | M00540 | GX12 male 5 pins output 45cm, panel mount (VFD, Laser) | 1.00 | M00353 | VFD - 2.2kW Inverter Control Unit | False
1 | M00010 | 5V Relay Module, 1 Channel | 1.00 | M00353 | VFD - 2.2kW Inverter Control Unit | False
1 | M00866 | Wago 5 connectors | 1.00 | M00353 | VFD - 2.2kW Inverter Control Unit | False
1 | M01697 | DIN912 M4x12 Black screw | 4.00 | M00353 | VFD - 2.2kW Inverter Control Unit | False
1 | M00746 | Rubber foot M4 | 4.00 | M00353 | VFD - 2.2kW Inverter Control Unit | False
1 | M01702 | Nut DIN934 M4 | 8.00 | M00353 | VFD - 2.2kW Inverter Control Unit | False
1 | M01715 | ISO 7380 M3x4 Black Screw | 6.00 | M00353 | VFD - 2.2kW Inverter Control Unit | False
1 | M00744 | Rocker switch DPST, panel mount | 1.00 | M00353 | VFD - 2.2kW Inverter Control Unit | False
1 | M00809 | Speakon Connector Panel Mount | 1.00 | M00353 | VFD - 2.2kW Inverter Control Unit | False
1 | M01237 | Blue Insulated Female Spade Connector, Receptacle, 4.8 x 0.5mm Tab Size, 1.5mm² to 2.5mm² | 3.00 | M00353 | VFD - 2.2kW Inverter Control Unit | False
1 | M00527 | Fork Spade Terminal 0.5mm² to 1.5mm², 22AWG to 16AWG, M4 Stud Size | 3.00 | M00353 | VFD - 2.2kW Inverter Control Unit | False
1 | M01533 | Dust Filter Mesh, 13cmx20cmx0.375mm, 0.5mm aperture | 2.00 | M00353 | VFD - 2.2kW Inverter Control Unit | False
1 | M01698 | DIN912 M4x16 Black screw | 4.00 | M00353 | VFD - 2.2kW Inverter Control Unit | False

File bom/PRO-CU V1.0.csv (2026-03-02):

level | component_reference | component_name | component_quantity | parent_bom_reference | parent_bom_name | has_child_bom
0 | M00298 | PRO - Control Unit | 1.00 |  |  | True
1 | M00218 | CNC Evo/Pro - Steel Parts - Control Unit Base | 1.00 | M00298 | PRO - Control Unit | False
1 | M00219 | CNC Evo/Pro - Steel Parts - Control Unit Cover | 1.00 | M00298 | PRO - Control Unit | False
1 | M00367 | CNC USB Controller Mk3/4 | 1.00 | M00298 | PRO - Control Unit | False
1 | M00368 | CNC USB Controller license | 1.00 | M00298 | PRO - Control Unit | False
1 | M00712 | Optocoupler 4 channels | 1.00 | M00298 | PRO - Control Unit | False
1 | M00663 | MicroSD 32GB Samsung Evo+ | 1.00 | M00298 | PRO - Control Unit | False
1 | M00751 | SMPS 600W 48V 12.5A (CNC Pro) | 1.00 | M00298 | PRO - Control Unit | False
1 | M00931 | SMPS 60W 24V 2.8A (CNC Pro/Fab) | 1.00 | M00298 | PRO - Control Unit | False
1 | M00853 | USB-C 24V to 5V 3A converter | 1.00 | M00298 | PRO - Control Unit | False
1 | M00502 | Ethernet RJ45 female 50cm, panel mount | 1.00 | M00298 | PRO - Control Unit | False
1 | M00542 | HDMI (female) panel mount to micro HDMI (male) | 1.00 | M00298 | PRO - Control Unit | False
1 | M00619 | PRO/FAB - Limit Switches PCB Assembly | 1.00 | M00298 | PRO - Control Unit | True
2 | M00714 | PCB Custom for CNC Limit Switches | 1.00 | M00619 | PRO/FAB - Limit Switches PCB Assembly | False
2 | M00841 | ALL - Tapped XLR 3 pole female panel, vertical PCB | 6.00 | M00619 | PRO/FAB - Limit Switches PCB Assembly | True
3 | M00917 | XLR 3 pole female panel, vertical PCB | 6.00 | M00841 | ALL - Tapped XLR 3 pole female panel, vertical PCB | False
2 | M00790 | Screw 2 Way PCB Terminal Block 5mm Pitch | 1.00 | M00619 | PRO/FAB - Limit Switches PCB Assembly | False
2 | M00791 | Screwless 4 Way PCB Terminal Block 3.5mm Pitch | 1.00 | M00619 | PRO/FAB - Limit Switches PCB Assembly | False
1 | M00536 | GX12 male 2 pins aux 45cm, panel mount (Emergency Button) | 1.00 | M00298 | PRO - Control Unit | False
1 | M00852 | USB-A male to A female panel mount, 30cm | 3.00 | M00298 | PRO - Control Unit | False
1 | M00073 | Axial Fan 24V 60x60mm, panel mount | 1.00 | M00298 | PRO - Control Unit | False
1 | M00514 | Fan cover 60mm | 1.00 | M00298 | PRO - Control Unit | False
1 | M00865 | Wago 3 connectors | 7.00 | M00298 | PRO - Control Unit | False
1 | M00866 | Wago 5 connectors | 4.00 | M00298 | PRO - Control Unit | False
1 | M01071 | Rubber foot M4 - Flat with Rivet | 4.00 | M00298 | PRO - Control Unit | False
1 | M00837 | TFHC M4x35 Black screw | 4.00 | M00298 | PRO - Control Unit | False
1 | M01715 | ISO 7380 M3x4 Black Screw | 40.00 | M00298 | PRO - Control Unit | False
1 | M00550 | Hex spacer M3x16 male/female | 2.00 | M00298 | PRO - Control Unit | False
1 | M00552 | Hex spacer M3x30 female/female | 2.00 | M00298 | PRO - Control Unit | False
1 | M00553 | Hex spacer M3x8 female/female | 8.00 | M00298 | PRO - Control Unit | False
1 | M01693 | ISO 7380 M3x10 Black Screw | 12.00 | M00298 | PRO - Control Unit | False
1 | M00984 | Female Banana Socket - Tab Termination | 1.00 | M00298 | PRO - Control Unit | False
1 | M01077 | GX12 male 3 pins aux 45cm, panel mount (Probe) | 1.00 | M00298 | PRO - Control Unit | False
1 | M01702 | Nut DIN934 M4 | 10.00 | M00298 | PRO - Control Unit | False
1 | M00739 | Raspberry Pi 4B 2G | 1.00 | M00298 | PRO - Control Unit | False
1 | M00540 | GX12 male 5 pins output 45cm, panel mount (VFD, Laser) | 2.00 | M00298 | PRO - Control Unit | False
1 | M00537 | GX12 male 2 pins aux 45cm, panel mount (Safety Enclosure) | 2.00 | M00298 | PRO - Control Unit | False
1 | M00530 | Fuse T slow 10A | 1.00 | M00298 | PRO - Control Unit | False
1 | M00744 | Rocker switch DPST, panel mount | 1.00 | M00298 | PRO - Control Unit | False
1 | M00689 | Motor Driver 2DM556S - PRO | 4.00 | M00298 | PRO - Control Unit | False
1 | M01729 | Dust Filter Mesh ("M"), 7cmx7cmx0.375mm, 0.5mm aperture | 1.00 | M00298 | PRO - Control Unit | False
1 | M00918 | XLR 4 pole female panel M3, Pre-wired 18cm breakout | 4.00 | M00298 | PRO - Control Unit | False
1 | M00559 | IDC Adapter PCB & Ribbon - 10-pin - 90° | 4.00 | M00298 | PRO - Control Unit | False
1 | M01070 | Insulated Crimp Bootlace Ferrule | 4.00 | M00298 | PRO - Control Unit | False
1 | M00107 | C14 Panel Mount 10A fuse | 1.00 | M00298 | PRO - Control Unit | False
1 | M01697 | DIN912 M4x12 Black screw | 6.00 | M00298 | PRO - Control Unit | False
1 | M00851 | USB-A USB-B cable 30cm Elbow type | 1.00 | M00298 | PRO - Control Unit | False
1 | M00407 | Coloured Washer M3 - Blue | 2.00 | M00298 | PRO - Control Unit | False
1 | M00408 | Coloured Washer M3 - Green | 3.00 | M00298 | PRO - Control Unit | False
1 | M00409 | Coloured Washer M3 - Red | 3.00 | M00298 | PRO - Control Unit | False
1 | M00410 | Coloured Washer M3 - Yellow | 2.00 | M00298 | PRO - Control Unit | False
1 | M00718 | PWM to Analog Voltage Converter 0-10V | 1.00 | M00298 | PRO - Control Unit | False

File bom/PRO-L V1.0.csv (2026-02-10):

level | component_reference | component_name | component_quantity | parent_bom_reference | parent_bom_name | has_child_bom
0 | M00656 | PRO-L [M0 Use] | 1.00 |  |  | True
1 | M00334 | PRO-L - Main Box 1/4 | 1.00 | M00656 | PRO-L [M0 Use] | True
2 | M00298 | PRO - Control Unit | 1.00 | M00334 | PRO-L - Main Box 1/4 | True
3 | M00218 | CNC Evo/Pro - Steel Parts - Control Unit Base | 1.00 | M00298 | PRO - Control Unit | False
3 | M00219 | CNC Evo/Pro - Steel Parts - Control Unit Cover | 1.00 | M00298 | PRO - Control Unit | False
3 | M00367 | CNC USB Controller Mk3/4 | 1.00 | M00298 | PRO - Control Unit | False
3 | M00368 | CNC USB Controller license | 1.00 | M00298 | PRO - Control Unit | False
3 | M00712 | Optocoupler 4 channels | 1.00 | M00298 | PRO - Control Unit | False
3 | M00663 | MicroSD 32GB Samsung Evo+ | 1.00 | M00298 | PRO - Control Unit | False
3 | M00751 | SMPS 600W 48V 12.5A (CNC Pro) | 1.00 | M00298 | PRO - Control Unit | False
3 | M00931 | SMPS 60W 24V 2.8A (CNC Pro/Fab) | 1.00 | M00298 | PRO - Control Unit | False
3 | M00853 | USB-C 24V to 5V 3A converter | 1.00 | M00298 | PRO - Control Unit | False
3 | M00502 | Ethernet RJ45 female 50cm, panel mount | 1.00 | M00298 | PRO - Control Unit | False
3 | M00542 | HDMI (female) panel mount to micro HDMI (male) | 1.00 | M00298 | PRO - Control Unit | False
3 | M00619 | PRO/FAB - Limit Switches PCB Assembly | 1.00 | M00298 | PRO - Control Unit | True
4 | M00714 | PCB Custom for CNC Limit Switches | 1.00 | M00619 | PRO/FAB - Limit Switches PCB Assembly | False
4 | M00841 | ALL - Tapped XLR 3 pole female panel, vertical PCB | 6.00 | M00619 | PRO/FAB - Limit Switches PCB Assembly | True
5 | M00917 | XLR 3 pole female panel, vertical PCB | 6.00 | M00841 | ALL - Tapped XLR 3 pole female panel, vertical PCB | False
4 | M00790 | Screw 2 Way PCB Terminal Block 5mm Pitch | 1.00 | M00619 | PRO/FAB - Limit Switches PCB Assembly | False
4 | M00791 | Screwless 4 Way PCB Terminal Block 3.5mm Pitch | 1.00 | M00619 | PRO/FAB - Limit Switches PCB Assembly | False
3 | M00536 | GX12 male 2 pins aux 45cm, panel mount (Emergency Button) | 1.00 | M00298 | PRO - Control Unit | False
3 | M00852 | USB-A male to A female panel mount, 30cm | 3.00 | M00298 | PRO - Control Unit | False
3 | M00073 | Axial Fan 24V 60x60mm, panel mount | 1.00 | M00298 | PRO - Control Unit | False
3 | M00514 | Fan cover 60mm | 1.00 | M00298 | PRO - Control Unit | False
3 | M00865 | Wago 3 connectors | 7.00 | M00298 | PRO - Control Unit | False
3 | M00866 | Wago 5 connectors | 4.00 | M00298 | PRO - Control Unit | False
3 | M01071 | Rubber foot M4 - Flat with Rivet | 4.00 | M00298 | PRO - Control Unit | False
3 | M00837 | TFHC M4x35 Black screw | 4.00 | M00298 | PRO - Control Unit | False
3 | M01715 | ISO 7380 M3x4 Black Screw | 40.00 | M00298 | PRO - Control Unit | False
3 | M00550 | Hex spacer M3x16 male/female | 2.00 | M00298 | PRO - Control Unit | False
3 | M00552 | Hex spacer M3x30 female/female | 2.00 | M00298 | PRO - Control Unit | False
3 | M00553 | Hex spacer M3x8 female/female | 8.00 | M00298 | PRO - Control Unit | False
3 | M01693 | ISO 7380 M3x10 Black Screw | 12.00 | M00298 | PRO - Control Unit | False
3 | M00984 | Female Banana Socket - Tab Termination | 1.00 | M00298 | PRO - Control Unit | False
3 | M01077 | GX12 male 3 pins aux 45cm, panel mount (Probe) | 1.00 | M00298 | PRO - Control Unit | False
3 | M01702 | Nut DIN934 M4 | 10.00 | M00298 | PRO - Control Unit | False
3 | M00739 | Raspberry Pi 4B 2G | 1.00 | M00298 | PRO - Control Unit | False
3 | M00540 | GX12 male 5 pins output 45cm, panel mount (VFD, Laser) | 2.00 | M00298 | PRO - Control Unit | False
3 | M00537 | GX12 male 2 pins aux 45cm, panel mount (Safety Enclosure) | 2.00 | M00298 | PRO - Control Unit | False
3 | M00530 | Fuse T slow 10A | 1.00 | M00298 | PRO - Control Unit | False
3 | M00744 | Rocker switch DPST, panel mount | 1.00 | M00298 | PRO - Control Unit | False
3 | M00689 | Motor Driver 2DM556S - PRO | 4.00 | M00298 | PRO - Control Unit | False
3 | M01729 | Dust Filter Mesh ("M"), 7cmx7cmx0.375mm, 0.5mm aperture | 1.00 | M00298 | PRO - Control Unit | False
3 | M00918 | XLR 4 pole female panel M3, Pre-wired 18cm breakout | 4.00 | M00298 | PRO - Control Unit | False
3 | M00559 | IDC Adapter PCB & Ribbon - 10-pin - 90° | 4.00 | M00298 | PRO - Control Unit | False
3 | M01070 | Insulated Crimp Bootlace Ferrule | 4.00 | M00298 | PRO - Control Unit | False
3 | M00107 | C14 Panel Mount 10A fuse | 1.00 | M00298 | PRO - Control Unit | False
3 | M01697 | DIN912 M4x12 Black screw | 6.00 | M00298 | PRO - Control Unit | False
3 | M00851 | USB-A USB-B cable 30cm Elbow type | 1.00 | M00298 | PRO - Control Unit | False
3 | M00407 | Coloured Washer M3 - Blue | 2.00 | M00298 | PRO - Control Unit | False
3 | M00408 | Coloured Washer M3 - Green | 3.00 | M00298 | PRO - Control Unit | False
3 | M00409 | Coloured Washer M3 - Red | 3.00 | M00298 | PRO - Control Unit | False
3 | M00410 | Coloured Washer M3 - Yellow | 2.00 | M00298 | PRO - Control Unit | False
3 | M00718 | PWM to Analog Voltage Converter 0-10V | 1.00 | M00298 | PRO - Control Unit | False
2 | M00335 | PRO-L - Mechanical Elements Box | 1.00 | M00334 | PRO-L - Main Box 1/4 | True
3 | M00063 | Angle Bracket 60 B-Type Groove 8 | 10.00 | M00335 | PRO-L - Mechanical Elements Box | False
3 | M00621 | Linear Block - H20B | 6.00 | M00335 | PRO-L - Mechanical Elements Box | False
3 | M00622 | Linear Block - W20A Block (Flange) | 4.00 | M00335 | PRO-L - Mechanical Elements Box | False
3 | M00704 | Nut Housing DSG16H | 4.00 | M00335 | PRO-L - Mechanical Elements Box | False
3 | M00511 | FF12 Bearing Support | 4.00 | M00335 | PRO-L - Mechanical Elements Box | False
3 | M00512 | FK12 Bearing Support | 4.00 | M00335 | PRO-L - Mechanical Elements Box | False
3 | M00301 | PRO - DIN912 M4x12 Black screw Bag | 1.00 | M00335 | PRO-L - Mechanical Elements Box | True
4 | M01697 | DIN912 M4x12 Black screw | 7.00 | M00301 | PRO - DIN912 M4x12 Black screw Bag | False
3 | M00302 | PRO - DIN912 M4x16 Black screw Bag | 1.00 | M00335 | PRO-L - Mechanical Elements Box | True
4 | M01698 | DIN912 M4x16 Black screw | 2.00 | M00302 | PRO - DIN912 M4x16 Black screw Bag | False
3 | M00303 | PRO - DIN912 M4x20 Black screw Bag | 1.00 | M00335 | PRO-L - Mechanical Elements Box | True
4 | M00430 | DIN912 M4x20 Black screw | 4.00 | M00303 | PRO - DIN912 M4x20 Black screw Bag | False
3 | M00304 | PRO - DIN912 M4x45 Black screw Bag | 1.00 | M00335 | PRO-L - Mechanical Elements Box | True
4 | M00432 | DIN912 M4x45 Black Screw | 11.00 | M00304 | PRO - DIN912 M4x45 Black screw Bag | False
3 | M00305 | PRO - DIN912 M4x55 Black screw Bag | 1.00 | M00335 | PRO-L - Mechanical Elements Box | True
4 | M00433 | DIN912 M4x55 Black Screw | 15.00 | M00305 | PRO - DIN912 M4x55 Black screw Bag | False
3 | M00306 | PRO - DIN912 M5x12 Black screw Bag | 1.00 | M00335 | PRO-L - Mechanical Elements Box | True
4 | M00435 | DIN912 M5x12 Black screw | 23.00 | M00306 | PRO - DIN912 M5x12 Black screw Bag | False
3 | M00307 | PRO - DIN912 M5x25 Black screw Bag | 1.00 | M00335 | PRO-L - Mechanical Elements Box | True
4 | M00439 | DIN912 M5x25 Black screw | 15.00 | M00307 | PRO - DIN912 M5x25 Black screw Bag | False
3 | M00308 | PRO - DIN912 M5x40 Black screw Bag | 1.00 | M00335 | PRO-L - Mechanical Elements Box | True
4 | M00442 | DIN912 M5x40 Black screw | 15.00 | M00308 | PRO - DIN912 M5x40 Black screw Bag | False
3 | M00309 | PRO - DIN912 M6x10 Black screw Bag | 1.00 | M00335 | PRO-L - Mechanical Elements Box | True
4 | M01716 | DIN912 M6x10 Black screw | 5.00 | M00309 | PRO - DIN912 M6x10 Black screw Bag | False
3 | M00310 | PRO - DIN912 M6x16 Black screw Bag | 1.00 | M00335 | PRO-L - Mechanical Elements Box | True
4 | M01704 | DIN912 M6x16 Black screw | 71.00 | M00310 | PRO - DIN912 M6x16 Black screw Bag | False
3 | M00311 | PRO - DIN912 M6x20 Black screw Bag | 1.00 | M00335 | PRO-L - Mechanical Elements Box | True
4 | M00451 | DIN912 M6x20 Black screw | 46.00 | M00311 | PRO - DIN912 M6x20 Black screw Bag | False
3 | M01646 | PRO - DIN912 M6x25 Screw Bag | 1.00 | M00335 | PRO-L - Mechanical Elements Box | True
4 | M01748 | DIN912 M6x25 Black screw | 4.00 | M01646 | PRO - DIN912 M6x25 Screw Bag | False
3 | M00312 | PRO - I-Type Sliding Nut M4 Bag | 1.00 | M00335 | PRO-L - Mechanical Elements Box | True
4 | M00554 | I-Type Sliding Nut M4 | 3.00 | M00312 | PRO - I-Type Sliding Nut M4 Bag | False
3 | M00315 | PRO - Lock Nut DIN985 M5 Bag | 1.00 | M00335 | PRO-L - Mechanical Elements Box | True
4 | M00632 | Lock Nut DIN985 M5 | 15.00 | M00315 | PRO - Lock Nut DIN985 M5 Bag | False
3 | M00316 | PRO - Lock Nut DIN985 M6 Bag | 1.00 | M00335 | PRO-L - Mechanical Elements Box | True
4 | M00630 | Lock Nut DIN985 M6 | 4.00 | M00316 | PRO - Lock Nut DIN985 M6 Bag | False
3 | M00314 | PRO - Lock Nut DIN985 M4 Bag | 1.00 | M00335 | PRO-L - Mechanical Elements Box | True
4 | M00629 | Lock Nut DIN985 M4 | 38.00 | M00314 | PRO - Lock Nut DIN985 M4 Bag | False
3 | M00313 | PRO - I-Type Sliding Nut M6 Bag | 1.00 | M00335 | PRO-L - Mechanical Elements Box | True
4 | M00556 | I-Type Sliding Nut M6 | 71.00 | M00313 | PRO - I-Type Sliding Nut M6 Bag | False
3 | M00299 | PRO - DIN9021 Washer M4x12 Bag | 1.00 | M00335 | PRO-L - Mechanical Elements Box | True
4 | M00423 | DIN9021 Washer M4x12 | 15.00 | M00299 | PRO - DIN9021 Washer M4x12 Bag | False
3 | M00300 | PRO - DIN9021 Washer M6x18 Bag | 1.00 | M00335 | PRO-L - Mechanical Elements Box | True
4 | M01694 | DIN9021 Washer M6x18 | 40.00 | M00300 | PRO - DIN9021 Washer M6x18 Bag | False
3 | M00317 | PRO - Spacer Bag - M5x19 | 1.00 | M00335 | PRO-L - Mechanical Elements Box | True
4 | M00795 | Spacer M5x19mm | 26.00 | M00317 | PRO - Spacer Bag - M5x19 | False
3 | M00318 | PRO - Spacer Bag - M5x30 | 1.00 | M00335 | PRO-L - Mechanical Elements Box | True
4 | M00796 | Spacer M5x30mm | 14.00 | M00318 | PRO - Spacer Bag - M5x30 | False
3 | M00319 | PRO - Spacer Bag - M6x90 | 1.00 | M00335 | PRO-L - Mechanical Elements Box | True
4 | M00800 | Spacer M6x90mm | 3.00 | M00319 | PRO - Spacer Bag - M6x90 | False
3 | M00321 | PRO - Mounting Tools Bag | 1.00 | M00335 | PRO-L - Mechanical Elements Box | True
4 | M00023 | Allen Key 2mm | 1.00 | M00321 | PRO - Mounting Tools Bag | False
4 | M00022 | Allen Key 2,5mm | 1.00 | M00321 | PRO - Mounting Tools Bag | False
4 | M00024 | Allen Key 3mm | 1.00 | M00321 | PRO - Mounting Tools Bag | False
4 | M00025 | Allen Key 4mm | 1.00 | M00321 | PRO - Mounting Tools Bag | False
4 | M00026 | Allen Key 5mm | 1.00 | M00321 | PRO - Mounting Tools Bag | False
4 | M00027 | Allen Key 6mm | 1.00 | M00321 | PRO - Mounting Tools Bag | False
4 | M00806 | Spanner 7mm | 1.00 | M00321 | PRO - Mounting Tools Bag | False
4 | M00807 | Spanner 8mm | 1.00 | M00321 | PRO - Mounting Tools Bag | False
4 | M00801 | Spanner 10mm | 1.00 | M00321 | PRO - Mounting Tools Bag | False
4 | M01681 | PRO - Acrylic Parts - L-shape Assembly Gauge | 1.00 | M00321 | PRO - Mounting Tools Bag | True
5 | M00716 | PMMA Sheet 3mm 600x400mm, Light Blue | 0.02 | M01681 | PRO - Acrylic Parts - L-shape Assembly Gauge | False
4 | M01682 | PRO - Acrylic Parts - U-shape Assembly Gauge | 1.00 | M00321 | PRO - Mounting Tools Bag | True
5 | M00716 | PMMA Sheet 3mm 600x400mm, Light Blue | 0.02 | M01682 | PRO - Acrylic Parts - U-shape Assembly Gauge | False
3 | M00320 | PRO - Miscellaneous Components Bag | 1.00 | M00335 | PRO-L - Mechanical Elements Box | True
4 | M00707 | Nylon Cap HP-30 | 3.00 | M00320 | PRO - Miscellaneous Components Bag | False
4 | M00389 | Cable Tie 100mm x 2.5 mm | 10.00 | M00320 | PRO - Miscellaneous Components Bag | False
4 | M00354 | CNC Pro/Fab - Steel Parts - Nut Offset | 4.00 | M00320 | PRO - Miscellaneous Components Bag | False
4 | M00364 | CNC Pro/Fab - Steels Parts - Bearing Support Offset Plate | 4.00 | M00320 | PRO - Miscellaneous Components Bag | False
4 | M00322 | CNC Pro - Steel Parts - Cable Chain Holder | 2.00 | M00320 | PRO - Miscellaneous Components Bag | False
4 | M00380 | Cable Chain TP15 End Connector (Female) | 2.00 | M00320 | PRO - Miscellaneous Components Bag | False
4 | M00381 | Cable Chain TP15 End Connector (Male) | 2.00 | M00320 | PRO - Miscellaneous Components Bag | False
4 | M00518 | Flexible Motor Coupler D25L30 - 6.35mm to 10mm | 4.00 | M00320 | PRO - Miscellaneous Components Bag | False
4 | M00887 | Wood screw 4x25mm | 4.00 | M00320 | PRO - Miscellaneous Components Bag | False
3 | M00331 | PRO-L - I-Type Sliding Nut M5 Bag | 1.00 | M00335 | PRO-L - Mechanical Elements Box | True
4 | M00555 | I-Type Sliding Nut M5 | 86.00 | M00331 | PRO-L - I-Type Sliding Nut M5 Bag | False
3 | M00329 | PRO-L - Black screw DIN912 M5x16 Bag | 1.00 | M00335 | PRO-L - Mechanical Elements Box | True
4 | M00437 | DIN912 M5x16 Black screw | 104.00 | M00329 | PRO-L - Black screw DIN912 M5x16 Bag | False
2 | M00330 | PRO-L - Electronic Components box | 1.00 | M00334 | PRO-L - Main Box 1/4 | True
3 | M01249 | PRO-L - Motor Cables | 1.00 | M00330 | PRO-L - Electronic Components box | True
4 | M00336 | PRO-L - BELRAM Motor Cables | 1.00 | M01249 | PRO-L - Motor Cables | True
5 | M00667 | Motor Cable X 250cm, Red (Pro-M/L) | 1.00 | M00336 | PRO-L - BELRAM Motor Cables | False
5 | M00673 | Motor Cable Y1 170cm, Green (Pro-M/L) | 1.00 | M00336 | PRO-L - BELRAM Motor Cables | False
5 | M00685 | Motor Cable Z 400cm, Blue (Pro-L) | 1.00 | M00336 | PRO-L - BELRAM Motor Cables | False
5 | M01755 | Motor Cable Y2 280cm, Yellow (Pro-L) | 1.00 | M00336 | PRO-L - BELRAM Motor Cables | False
4 | M00974 | Cable Tie 385mm x 4.8 mm, Blue | 1.00 | M01249 | PRO-L - Motor Cables | False
4 | M00659 | Micro-Fit 3.0 Female Connector Housing | 4.00 | M01249 | PRO-L - Motor Cables | False
4 | M00661 | Micro-Fit Female Crimp Terminal Contact | 14.00 | M01249 | PRO-L - Motor Cables | False
3 | M00696 | ALL - Nema23 Motor | 4.00 | M00330 | PRO-L - Electronic Components box | True
4 | M00697 | Nema23 Stepper Motor 5A 6.35mm Shaft | 4.00 | M00696 | ALL - Nema23 Motor | False
4 | M00660 | Micro-Fit 3.0 Male Connector Housing | 4.00 | M00696 | ALL - Nema23 Motor | False
4 | M00662 | Micro-Fit Male Crimp Terminal Contact | 14.00 | M00696 | ALL - Nema23 Motor | False
3 | M00332 | PRO-L - Inductive Sensor Cables | 1.00 | M00330 | PRO-L - Electronic Components box | True
4 | M01754 | Inductive Sensor Cable Y2- 210cm Yellow (Pro-L) | 1.00 | M00332 | PRO-L - Inductive Sensor Cables | False
4 | M00586 | Inductive Sensor Cable Y1- 130cm Green (Pro-S/M/L) | 1.00 | M00332 | PRO-L - Inductive Sensor Cables | True
5 | M00569 | Inductive Sensor Cable Unterminated 120cm | 1.00 | M00586 | Inductive Sensor Cable Y1- 130cm Green (Pro-S/M/L) | False
4 | M00585 | Inductive Sensor Cable Y1+ 170cm Green (Pro-M/L) | 1.00 | M00332 | PRO-L - Inductive Sensor Cables | True
5 | M00576 | Inductive Sensor Cable Unterminated 160cm | 1.00 | M00585 | Inductive Sensor Cable Y1+ 170cm Green (Pro-M/L) | False
4 | M00581 | Inductive Sensor Cable X+ 390cm Red (Pro-L) | 1.00 | M00332 | PRO-L - Inductive Sensor Cables | True
5 | M00574 | Inductive Sensor Cable Unterminated 390cm | 1.00 | M00581 | Inductive Sensor Cable X+ 390cm Red (Pro-L) | False
4 | M00583 | Inductive Sensor Cable X- 240cm Red (Pro-M/L) | 1.00 | M00332 | PRO-L - Inductive Sensor Cables | True
5 | M00572 | Inductive Sensor Cable Unterminated 240cm | 1.00 | M00583 | Inductive Sensor Cable X- 240cm Red (Pro-M/L) | False
4 | M00590 | Inductive Sensor Cable Z+ 410cm Blue (Pro-L) | 1.00 | M00332 | PRO-L - Inductive Sensor Cables | True
5 | M00578 | Inductive Sensor Cable Unterminated 410cm | 1.00 | M00590 | Inductive Sensor Cable Z+ 410cm Blue (Pro-L) | False
4 | M01001 | CNC Pro-L - Belram lot of Sensor Cables | 1.00 | M00332 | PRO-L - Inductive Sensor Cables | False
4 | M00974 | Cable Tie 385mm x 4.8 mm, Blue | 1.00 | M00332 | PRO-L - Inductive Sensor Cables | False
4 | M00975 | Cable Tie 200mm x 4.6 mm, Orange | 1.00 | M00332 | PRO-L - Inductive Sensor Cables | False
3 | M00591 | Inductive Sensor PNP NC, M12 | 6.00 | M00330 | PRO-L - Electronic Components box | False
3 | M01078 | Touch Probe Z Device (3-pins model) | 1.00 | M00330 | PRO-L - Electronic Components box | False
3 | M00482 | Emergency Stop Button 1NC | 1.00 | M00330 | PRO-L - Electronic Components box | False
3 | M00007 | Power Cable C13 IEC to CEE 7/4, Schuko, 2m, 10 A, 250 V | 1.00 | M00330 | PRO-L - Electronic Components box | False
3 | M00848 | USB Key 2Gb | 1.00 | M00330 | PRO-L - Electronic Components box | False
2 | M00823 | Square Plate - First CNC Test | 1.00 | M00334 | PRO-L - Main Box 1/4 | False
2 | M00215 | EVO/PRO - Interface Unit | 1.00 | M00334 | PRO-L - Main Box 1/4 | True
3 | M00189 | CNC Evo/Pro - Steel Parts - Interface Unit Base | 1.00 | M00215 | EVO/PRO - Interface Unit | False
3 | M00190 | CNC Evo/Pro - Steel Parts - Interface Unit Cover | 1.00 | M00215 | EVO/PRO - Interface Unit | False
3 | M00011 | 7" LCD Touch Screen 1024x600 TFT | 1.00 | M00215 | EVO/PRO - Interface Unit | False
3 | M00700 | Numeric Keypad 34 Keys | 1.00 | M00215 | EVO/PRO - Interface Unit | False
3 | M01715 | ISO 7380 M3x4 Black Screw | 8.00 | M00215 | EVO/PRO - Interface Unit | False
3 | M00842 | Tooth Lock Washer DIN6798 M6 Type A Black | 8.00 | M00215 | EVO/PRO - Interface Unit | False
3 | M01698 | DIN912 M4x16 Black screw | 2.00 | M00215 | EVO/PRO - Interface Unit | False
3 | M01704 | DIN912 M6x16 Black screw | 2.00 | M00215 | EVO/PRO - Interface Unit | False
3 | M00543 | HDMI Cable Male/Male 1.5m | 1.00 | M00215 | EVO/PRO - Interface Unit | False
3 | M00849 | USB-A Micro USB Cable 1.5m | 1.00 | M00215 | EVO/PRO - Interface Unit | False
3 | M01637 | INT - Fixation Bag | 1.00 | M00215 | EVO/PRO - Interface Unit | True
4 | M01636 | Spacer M6x16 | 2.00 | M01637 | INT - Fixation Bag | False
4 | M01694 | DIN9021 Washer M6x18 | 2.00 | M01637 | INT - Fixation Bag | False
4 | M00556 | I-Type Sliding Nut M6 | 2.00 | M01637 | INT - Fixation Bag | False
4 | M01748 | DIN912 M6x25 Black screw | 2.00 | M01637 | INT - Fixation Bag | False
3 | M00716 | PMMA Sheet 3mm 600x400mm, Light Blue | 1.00 | M00215 | EVO/PRO - Interface Unit | False
3 | M00461 | Disc Magnet Ø 10mm, height 3mm | 3.00 | M00215 | EVO/PRO - Interface Unit | False
3 | M01675 | DIN912 M4x25 Black screw | 2.00 | M00215 | EVO/PRO - Interface Unit | False
3 | M01534 | Male USB-A to Male USB-C Cable 150cm | 1.00 | M00215 | EVO/PRO - Interface Unit | False
1 | M00222 | EVO/PRO-L - Structure Box 2/2 | 1.00 | M00656 | PRO-L [M0 Use] | True
2 | M00055 | Alu Profile V-3030 (240mm) [1x M6 thread on BOTH sides] | 2.00 | M00222 | EVO/PRO-L - Structure Box 2/2 | False
2 | M00034 | Alu Profile I-6030 (1020 mm) | 2.00 | M00222 | EVO/PRO-L - Structure Box 2/2 | False
2 | M00035 | Alu Profile I-6030 (1170 mm) | 3.00 | M00222 | EVO/PRO-L - Structure Box 2/2 | False
2 | M00056 | Alu Profile V-6060 (1230 mm) [4x M6 threads on BOTH sides] | 3.00 | M00222 | EVO/PRO-L - Structure Box 2/2 | False
2 | M00374 | Cable Chain 900mm (Evo/Pro-S/M/L) | 1.00 | M00222 | EVO/PRO-L - Structure Box 2/2 | False
2 | M00372 | Cable Chain 1325mm (Evo/Pro-L) | 1.00 | M00222 | EVO/PRO-L - Structure Box 2/2 | False
1 | M00333 | PRO-L - Linear Motion Box 3/4 | 1.00 | M00656 | PRO-L [M0 Use] | True
2 | M00056 | Alu Profile V-6060 (1230 mm) [4x M6 threads on BOTH sides] | 1.00 | M00333 | PRO-L - Linear Motion Box 3/4 | False
2 | M00082 | Ballscrew SFU1610 1200mm & Nut | 3.00 | M00333 | PRO-L - Linear Motion Box 3/4 | False
2 | M00081 | Ballscrew SFU1605 250mm & Nut | 1.00 | M00333 | PRO-L - Linear Motion Box 3/4 | False
2 | M00623 | Linear Rail HGR20 (1200mm) | 4.00 | M00333 | PRO-L - Linear Motion Box 3/4 | False
2 | M00624 | Linear Rail HGR20 (200mm) | 2.00 | M00333 | PRO-L - Linear Motion Box 3/4 | False
2 | M00070 | PRO - Anti-slip Cover, I-type Alu Profile 1200mm | 4.00 | M00333 | PRO-L - Linear Motion Box 3/4 | True
3 | M00069 | Anti-slip Cover, I-type Alu Profile | 4.80 | M00070 | PRO - Anti-slip Cover, I-type Alu Profile 1200mm | False
2 | M00382 | PRO-L - Cable Cover for I-type 6 Profile 1200mm | 1.00 | M00333 | PRO-L - Linear Motion Box 3/4 | True
3 | M00383 | Cable Cover for I-type 6 Profile (2m) | 0.60 | M00382 | PRO-L - Cable Cover for I-type 6 Profile 1200mm | False
2 | M00294 | CNC Pro - 2020 Profile Assembly Gauge - 200mm | 2.00 | M00333 | PRO-L - Linear Motion Box 3/4 | False
1 | M00325 | PRO - Steel Parts Box 4/4 | 1.00 | M00656 | PRO-L [M0 Use] | True
2 | M00323 | CNC Pro - Steel Parts - Y Foot Frame | 4.00 | M00325 | PRO - Steel Parts Box 4/4 | False
2 | M00324 | CNC Pro - Steel Parts - Y Gantry | 2.00 | M00325 | PRO - Steel Parts Box 4/4 | False
2 | M00360 | CNC Pro/Fab - Steel Parts - X Nut | 1.00 | M00325 | PRO - Steel Parts Box 4/4 | False
2 | M00358 | CNC Pro/Fab - Steel Parts - Z-Axis Bottom Bearing Plate | 1.00 | M00325 | PRO - Steel Parts Box 4/4 | False
2 | M00361 | CNC Pro/Fab - Steel Parts - Z Plate | 1.00 | M00325 | PRO - Steel Parts Box 4/4 | False
2 | M00359 | CNC Pro/Fab - Steel Parts - Z-axis Top Motor Plate | 1.00 | M00325 | PRO - Steel Parts Box 4/4 | False

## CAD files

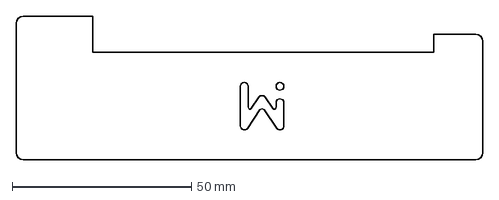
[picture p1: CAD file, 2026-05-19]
cad/PRO Mounting Gauge 01.dxf
130.0 x 40.0 mm

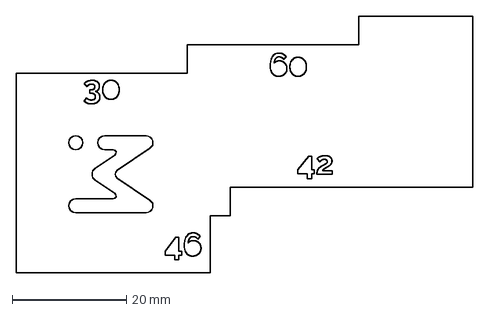
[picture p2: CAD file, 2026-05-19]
cad/PRO Mounting Gauge 02.dxf
80.0 x 45.0 mm

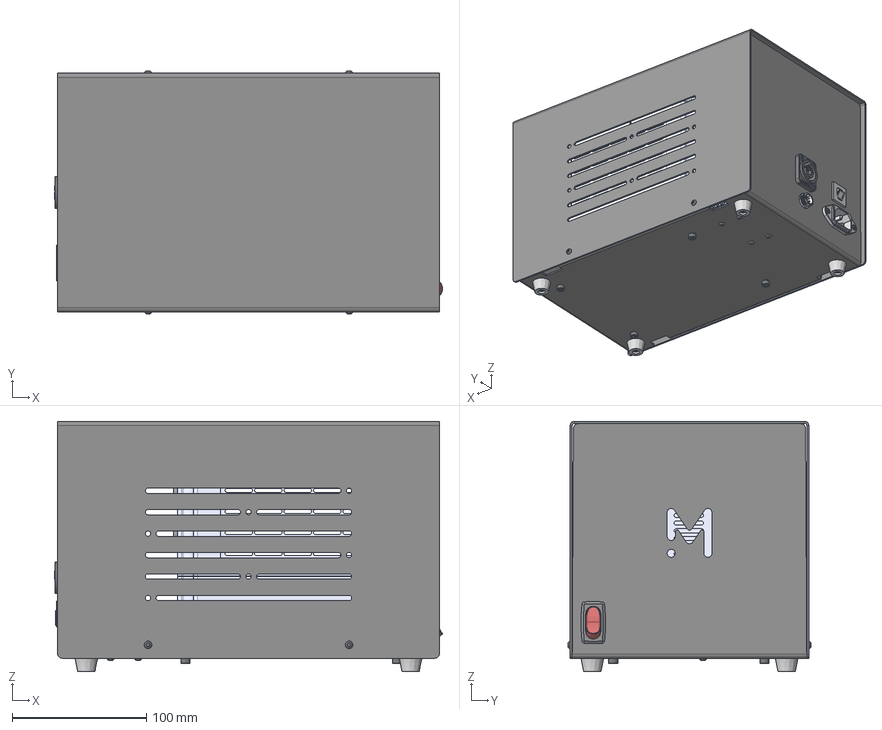
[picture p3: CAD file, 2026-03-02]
cad/VFD-CU V1.2.stp
289.5 x 181.3 x 186.8 mm
Hex Spacer F/F Threaded M3 (parametric) x 4
M4x12 - DIN912 x 8
DIN 934 Nut M4_1 x 8
M3x6 - ISO7380 x 16
Base
Broaching Nut M3 (kf2-m3-et) x 8
Cover
Défaut
5V One Channel Relay
C14 IEC Male Panel Mount with RFI Filter
Thermal Circuit Breaker 15A 250V AC
DPST Rocker Switch
Nut M12x0.75 H=1.8mm v2
Rubber Foot M4 x 4

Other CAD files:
cad/Cable Clip for I-type Groove 6mm.step
cad/PRO-S V1.0.step
cad/PRO-CU V1.0.step
cad/PRO-L V1.0.step
cad/PRO-M V1.0.step

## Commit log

2026-02-10 Initial commit with all current files
    [PRO-CU V1.0.step, PRO-L V1.0.csv, PRO-L V1.0.step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]
2026-03-02 Added VFD control unit CAD file
    [VFD-CU V1.2.stp]
2026-03-02 Update of the BOM: PRO-CU V1.0
    SKU: M00298
    File: PRO-CU V1.0.csv
    Synced at: Mon Mar 2 07:55:36 UTC 2026
    [PRO-CU V1.0.csv]
2026-03-02 Update of the BOM: VFD-CU V1.2
    SKU: M00353
    File: VFD-CU V1.2.csv
    Synced at: Mon Mar 2 08:38:26 UTC 2026
    [VFD-CU V1.2.csv]
